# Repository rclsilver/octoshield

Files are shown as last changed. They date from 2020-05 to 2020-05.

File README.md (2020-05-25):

# OctoShield

This Raspberry pi hat can be used with [OctoPrint-Enclosure](https://plugins.octoprint.org/plugins/enclosure/) plugin.

This hat is compatible with Raspberry Pi 2, 3 or 4.

With this hat, you will be able to:
* manage a 30x30 5V fan to regulate the Raspberry Pi temperature
* manage a dual relay module for printer power and a LED strip
* read the temperature of your enclosure with a [DS18B20](https://datasheets.maximintegrated.com/en/ds/DS18B20.pdf) sensor
* cut the power of your printer when some smoke is detected by an external smoke detector or when you press an emergency button

All connectors are [JST XH](https://www.jst-mfg.com/product/pdf/eng/eXH.pdf) to be easier to use.

## Inputs / Outputs

* `GPIO.5` (Output): The fan
* `GPIO.7` (Input): The [DS18B20](https://datasheets.maximintegrated.com/en/ds/DS18B20.pdf) sensor
* `GPIO.27` (Input): The power button to toggle printer power
* `GPIO.17` (Output): The signal to the relay which manages the printer power
* `GPIO.4` (Input): The LED button to toggle LED strip power
* `GPIO.3` (Output): The signal to the relay which manages the LED strip power
* `GPIO. 6` (Input): The emergency signal to turn off the printer power

## Power

The board works with a *5V DC* power. The power supply must be connected to `J1` connector:

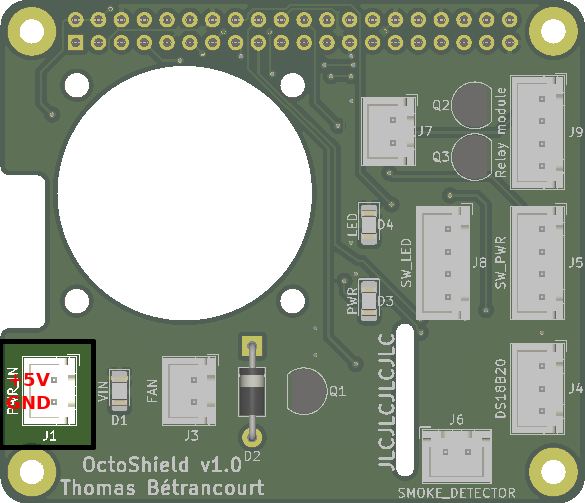
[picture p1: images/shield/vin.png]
shield_vin


## Fan

The fan must be connected to `J3` connector:

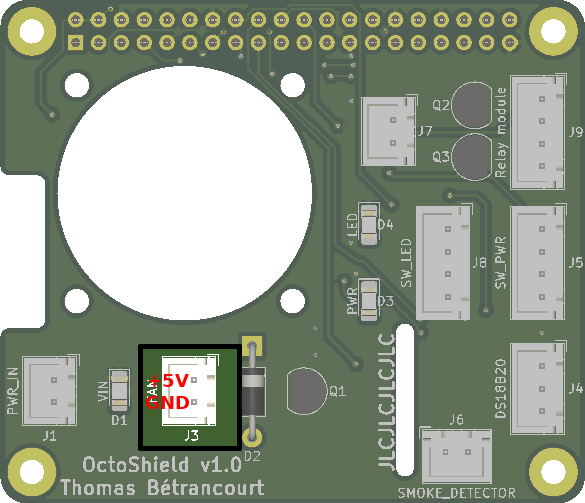
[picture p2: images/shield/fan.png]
shield_fan


The fan can be controlled with the `GPIO.5`. A *HIGH* level turn on the fan.

You can use the provided [script](/fan-control/fan-control.py) and [SystemD service](/fan-control/fan-control.service) to manage the regulate the temperature.

You must use the [SSH](https://www.raspberrypi.org/documentation/remote-access/ssh/) access to enable the service by executing following commands with the `pi` user:

```shell
git clone https://github.com/rclsilver/octoshield.git
sudo cp octoshield/fan-control/fan-control.py /usr/local/bin
sudo cp octoshield/fan-control/fan-control.service /etc/systemd/system/
sudo systemctl daemon-reload
sudo systemctl enable fan-control.service
sudo systemctl start fan-control.service
```

## Temperature sensor

The sensor must be connected to `J4` connector:

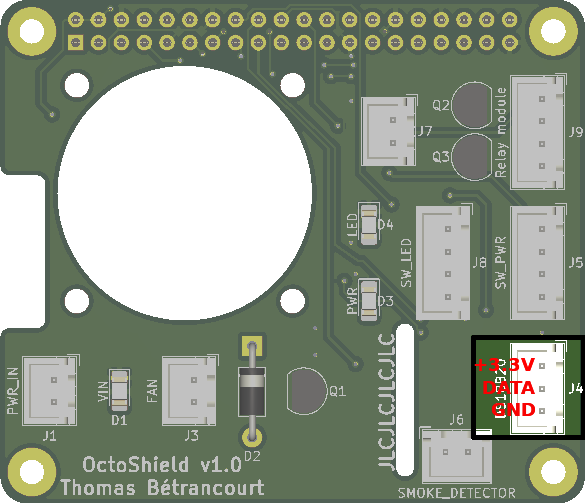
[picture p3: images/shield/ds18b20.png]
shield_ds18b20


Temperature sensor [DS18B20](https://datasheets.maximintegrated.com/en/ds/DS18B20.pdf) can be used with the [1-Wire](https://en.wikipedia.org/wiki/1-Wire) protocol on a Raspberry Pi.

You must enable this interface to be used with the [SSH](https://www.raspberrypi.org/documentation/remote-access/ssh/) access by executing following commands with the `pi` user:

```shell
sudo raspi-config
```

*Note*: Use the direction arrows to navigate in the menu and the *Enter* key to validate.

1. Enter in the `Interfacing Options` menu
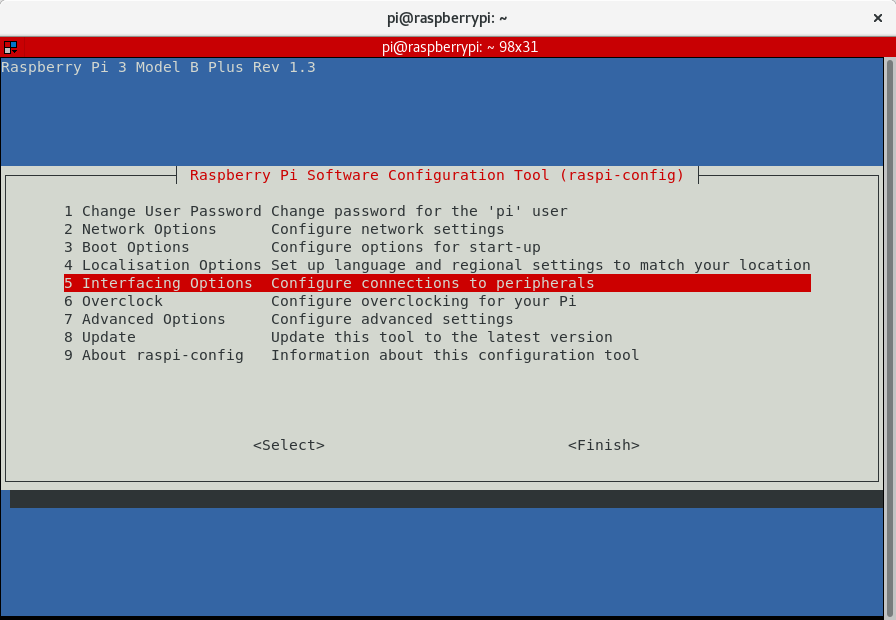
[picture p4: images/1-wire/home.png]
raspi-config_home


1. Enter in the `1-Wire` submenu
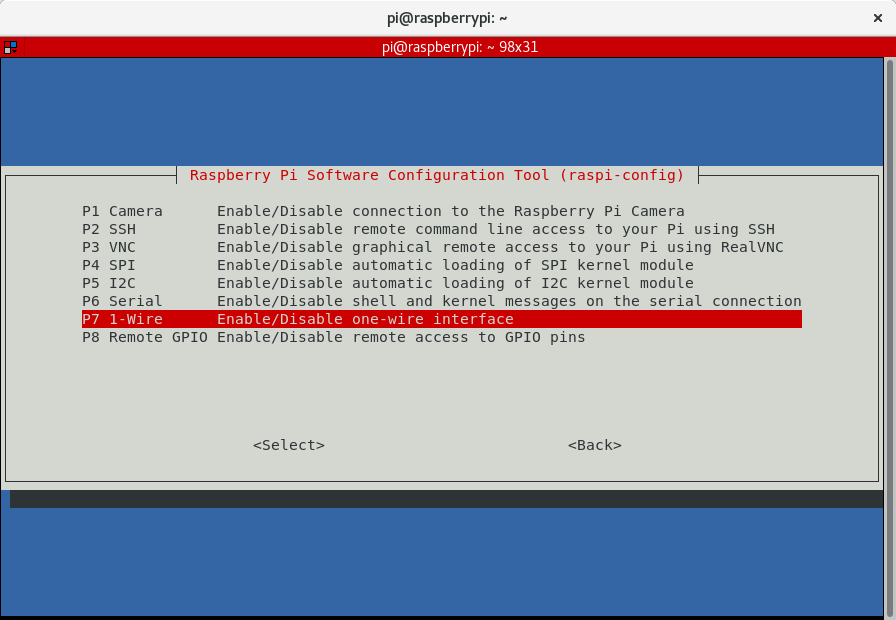
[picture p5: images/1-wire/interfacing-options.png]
raspi-config_interfacing-options


1. Select `Yes` and press the *Enter* key
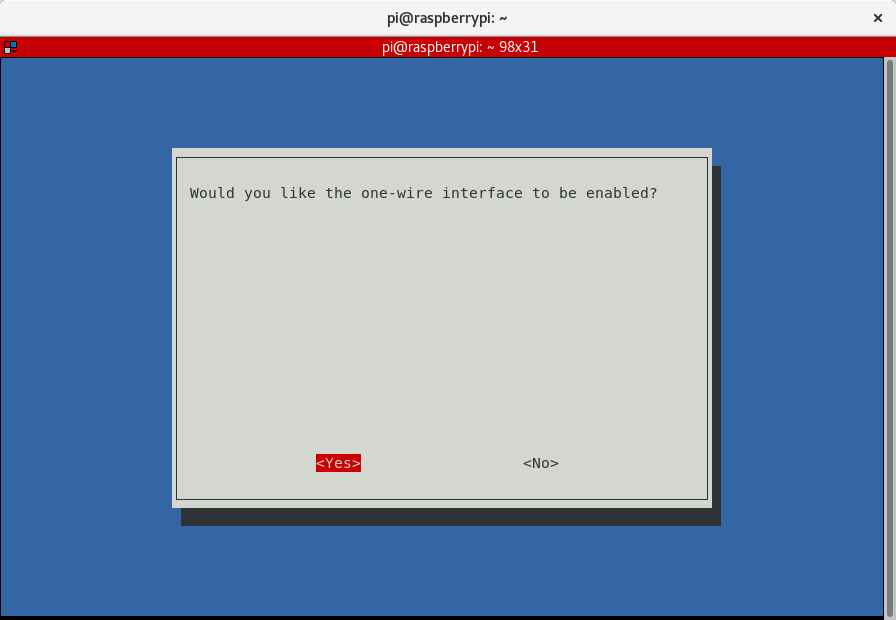
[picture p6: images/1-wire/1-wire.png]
raspi-config_1-wire


1. The interface has been enabled, you can press *Enter* to continue
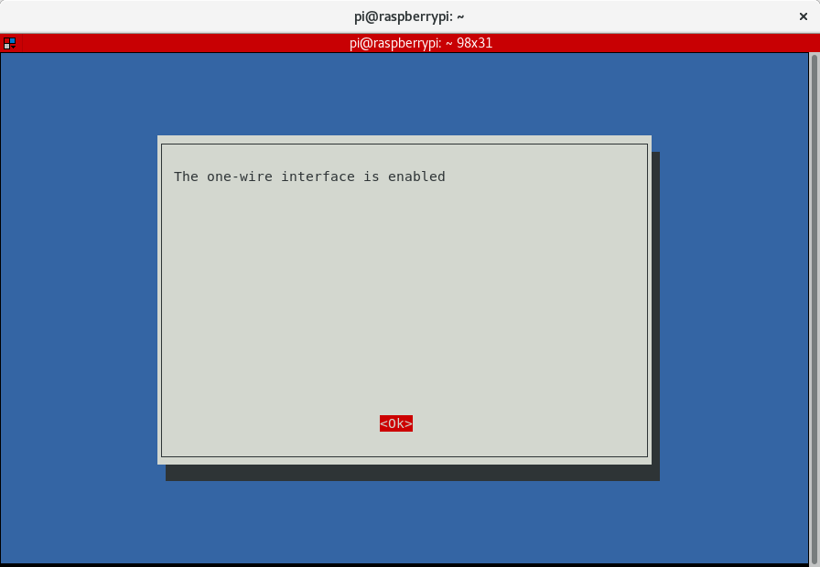
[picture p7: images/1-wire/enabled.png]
raspi-config_enabled


1. You can now select `Finish` with the *Right arrow* key
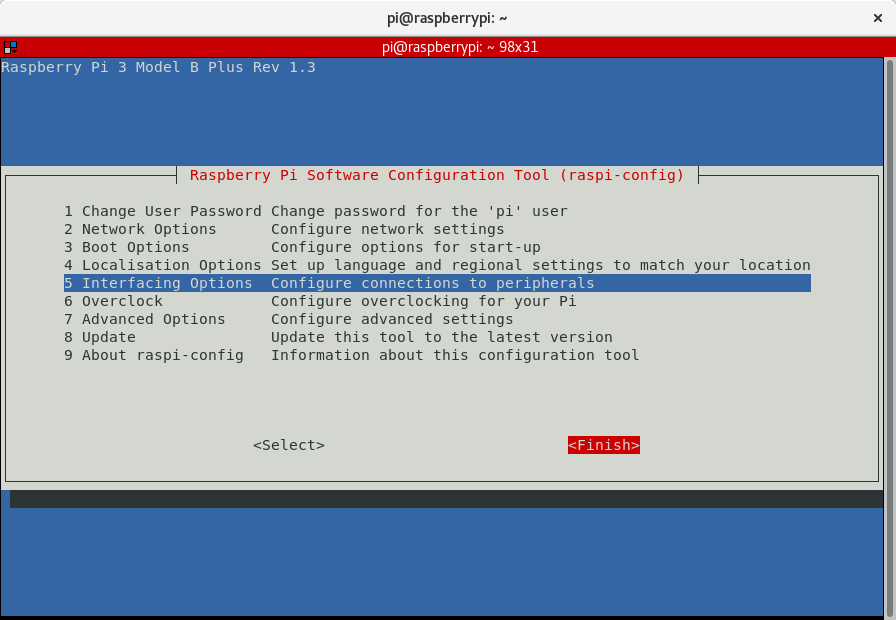
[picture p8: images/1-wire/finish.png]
raspi-config_finish


1. You have to reboot the Raspberry pi
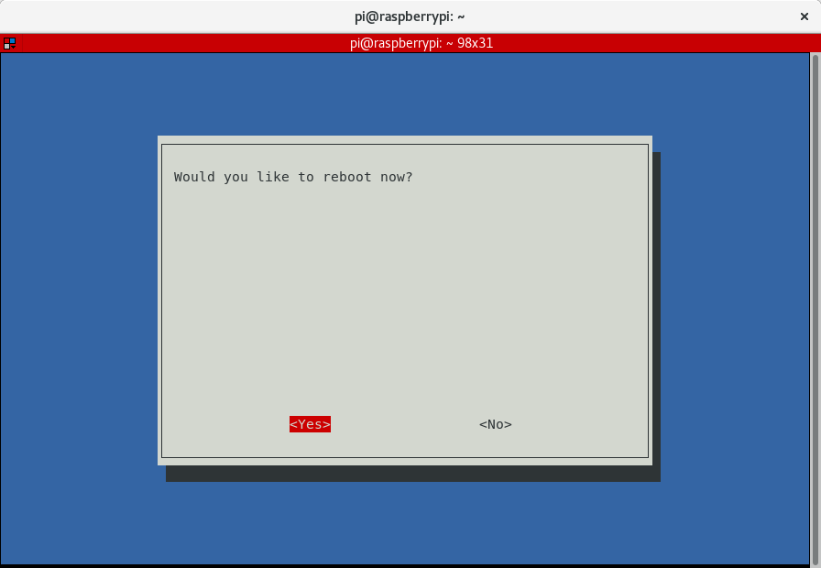
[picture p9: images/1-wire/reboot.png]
raspi-config_reboot


You will need to obtain your temperature device id by executing the following command:

```shell
cat /sys/devices/w1_bus_master1/*/name
```

This will print the ID if all is working fine. If nothing is printed, please check your installation.

Now, in the [OctoPrint-Enclosure](https://plugins.octoprint.org/plugins/enclosure/) plugin settings, you can add your sensor by adding a new Input and following this screenshot:

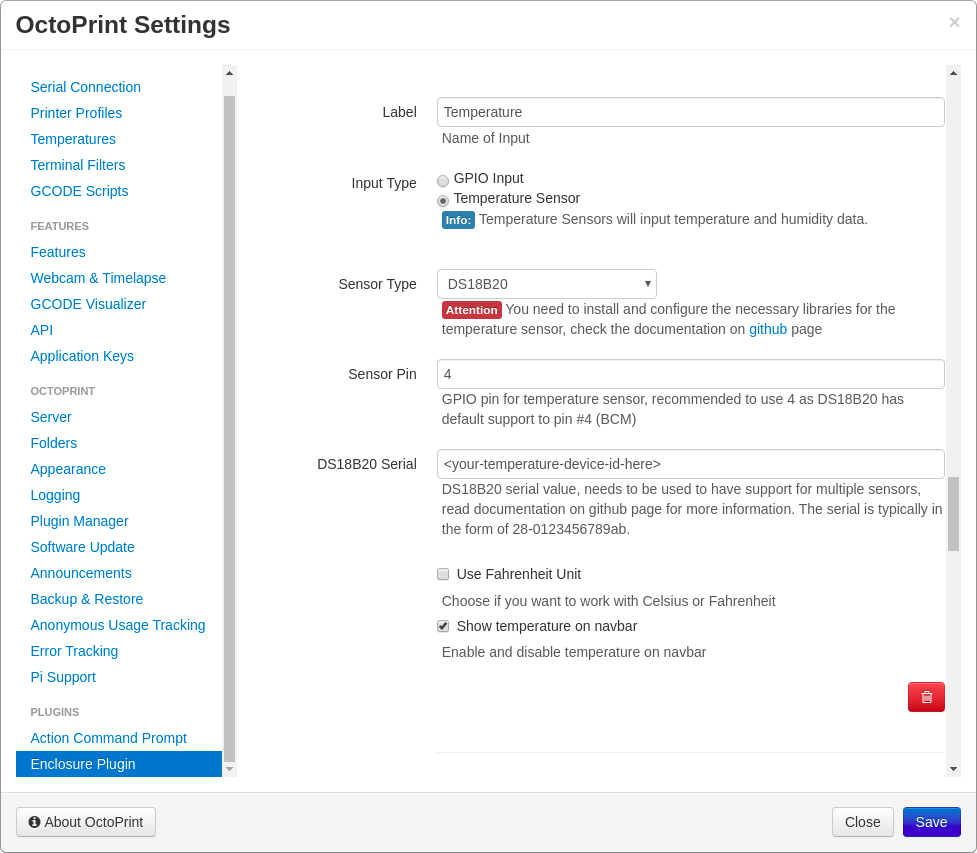
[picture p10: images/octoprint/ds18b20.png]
octoprint_ds18b20


## Printer power

The power switch must be connected to `J5` connector:

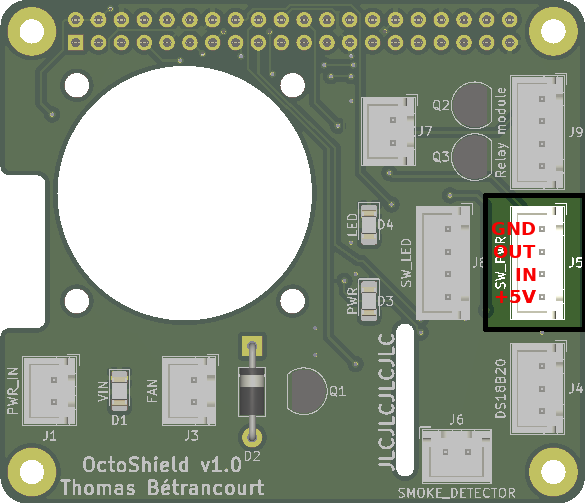
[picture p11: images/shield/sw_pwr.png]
shield_sw_pwr


When `+5V` and `IN` pins are connected, a *LOW* level is transmitted to the `PWR` pin of `J9` and power of printer is turned on. In this case, `OUT` pin is powered by a *5V DC* power to turn on a light signal.

### OctoPrint

Now, in the [OctoPrint-Enclosure](https://plugins.octoprint.org/plugins/enclosure/) plugin settings, you can manage the printer power relay following those screenshots.

#### Input

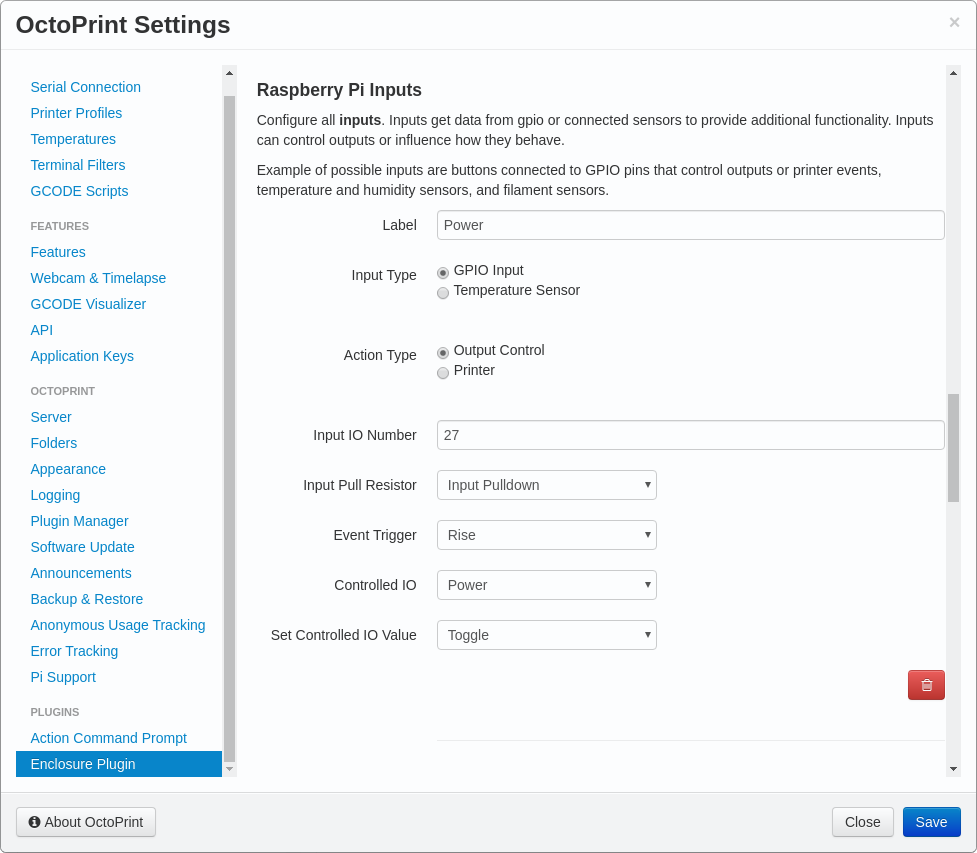
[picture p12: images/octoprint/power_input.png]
octoprint_pwr_input


#### Output

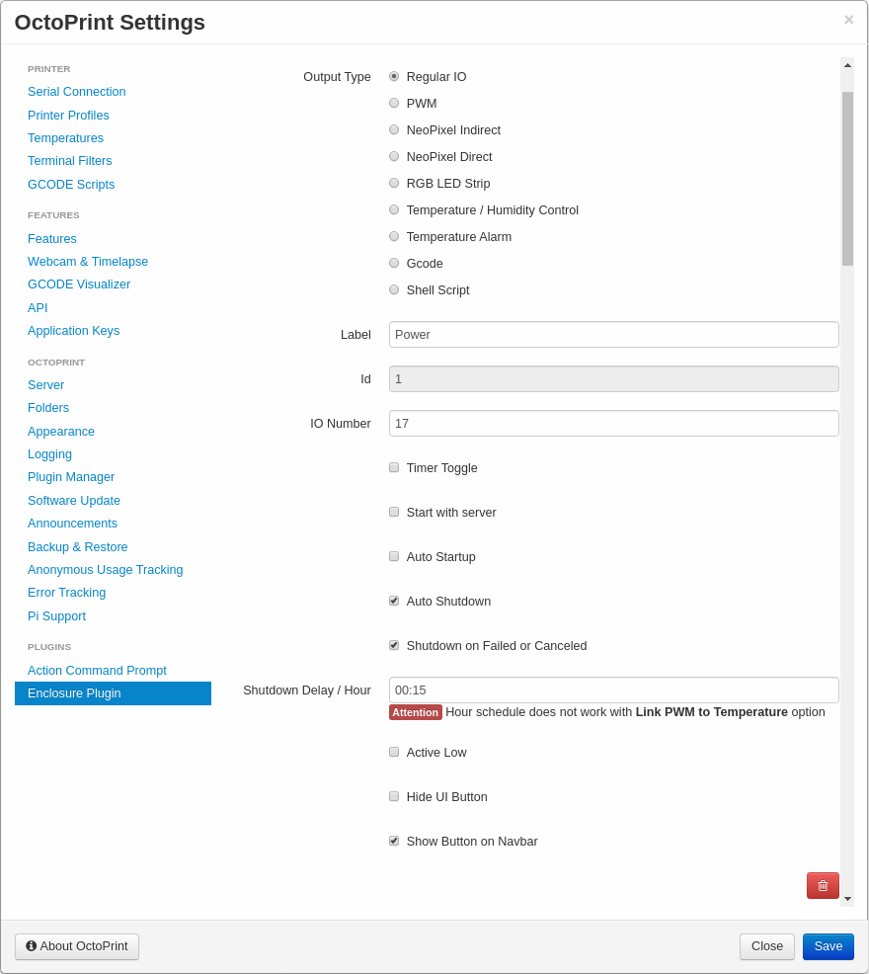
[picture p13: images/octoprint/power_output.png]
octoprint_pwr_output


## LED strip power

The LED strip switch must be connected to `J8` connector:

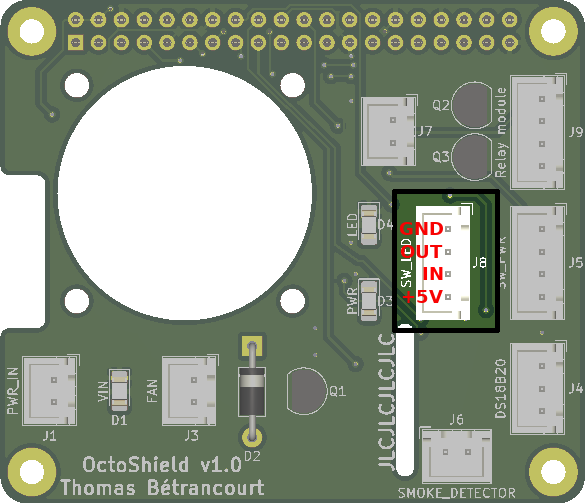
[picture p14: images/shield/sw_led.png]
shield_sw_led


When `+5V` and `IN` pins are connected, a *LOW* level is transmitted to the `LED` pin of `J9` and power of LED strip is turned on. In this case, `OUT` pin is powered by a *5V DC* power to turn on a light signal.

### OctoPrint

Now, in the [OctoPrint-Enclosure](https://plugins.octoprint.org/plugins/enclosure/) plugin settings, you can manage the LED strip power relay following those screenshots.

#### Input

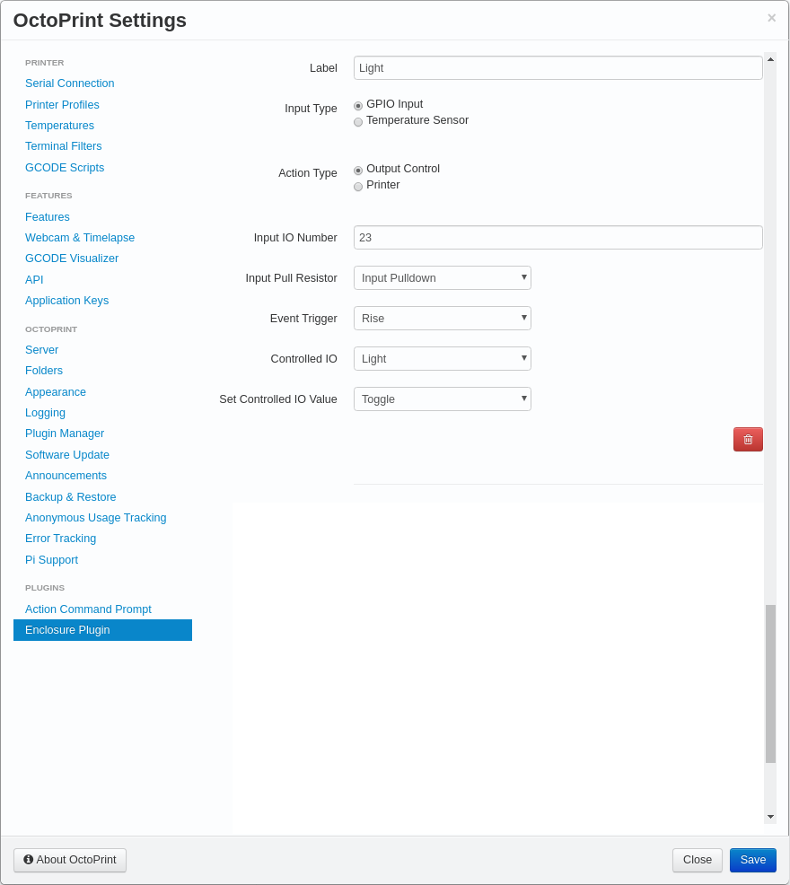
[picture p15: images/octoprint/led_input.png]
octoprint_led_input


#### Output

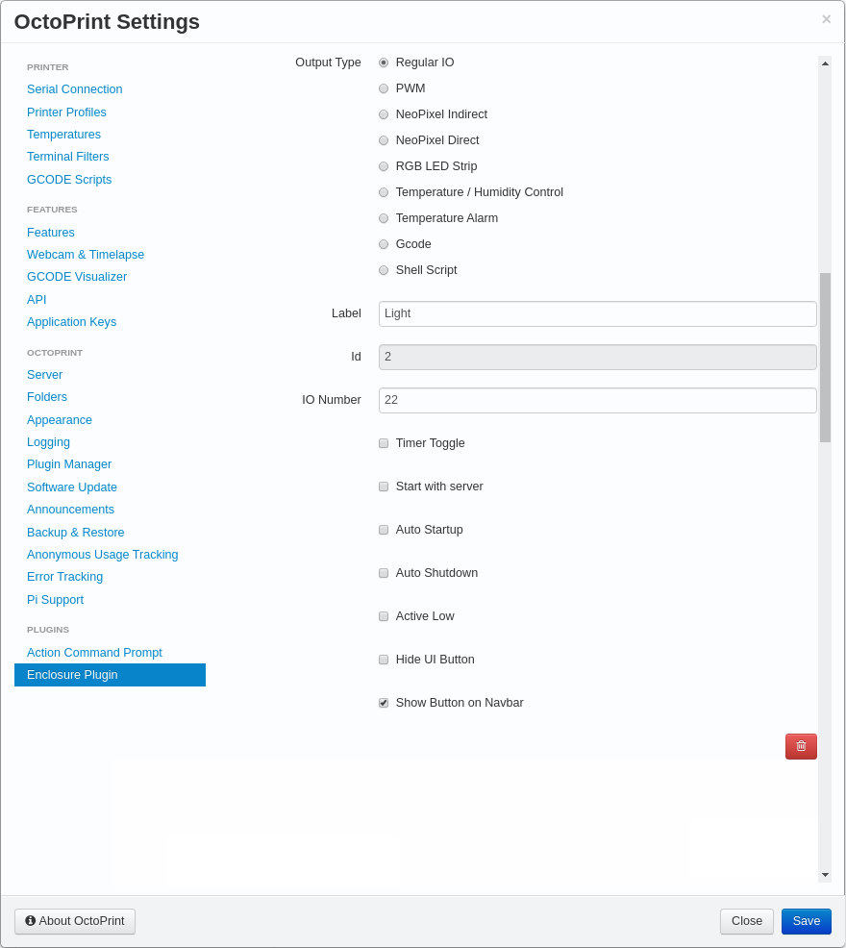
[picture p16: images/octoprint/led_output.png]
octoprint_led_output


## Smoke detector / Emergency button

You can use both a smoke detector or an emergency button to power down the printer.

### Smoke detector

Most of detectors send *9V DC* power when it detects some smoke. You must find points on your and connect them on `J8` connector:

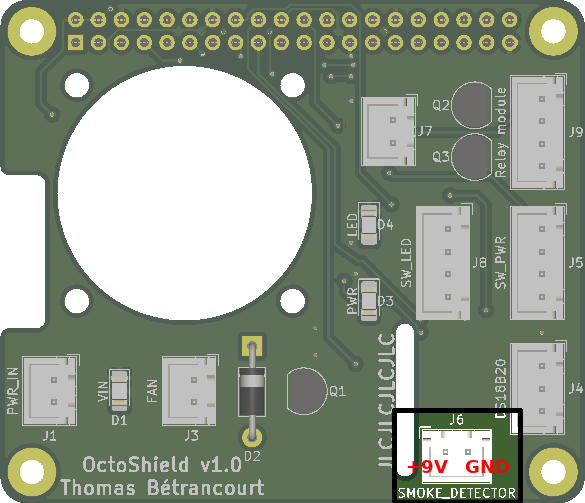
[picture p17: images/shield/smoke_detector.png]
shield_smoke_detector


When the detector is detecting smoke, a *HIGH* level is transmitted to the `GPIO.6`. You have to tell OctoPrint to turn off the printer.

### Emergency button

The emergency button must be connected to `J7` connector:

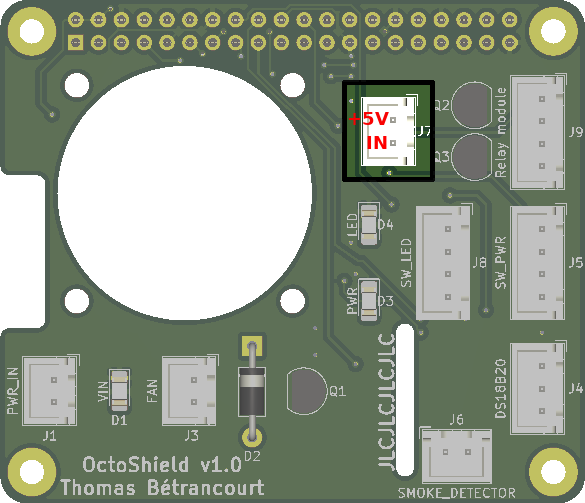
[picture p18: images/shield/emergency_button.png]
shield_sw_led


When `+5V` and `IN` pins are connected, a *HIGH* level is transmitted to the `GPIO.6`. You have to tell OctoPrint to turn off the printer.

### OctoPrint

Now, in the [OctoPrint-Enclosure](https://plugins.octoprint.org/plugins/enclosure/) plugin settings, you can add your emergency input following this screenshot.

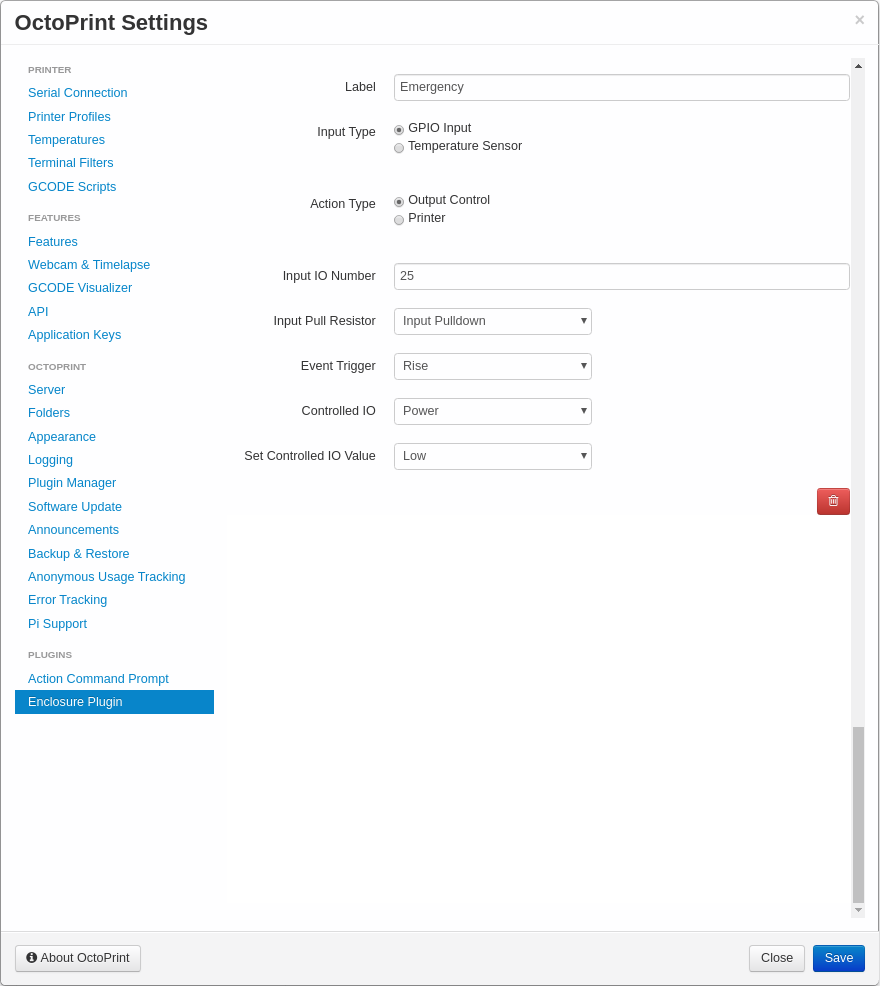
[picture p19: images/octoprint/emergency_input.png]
octoprint_emergency_input


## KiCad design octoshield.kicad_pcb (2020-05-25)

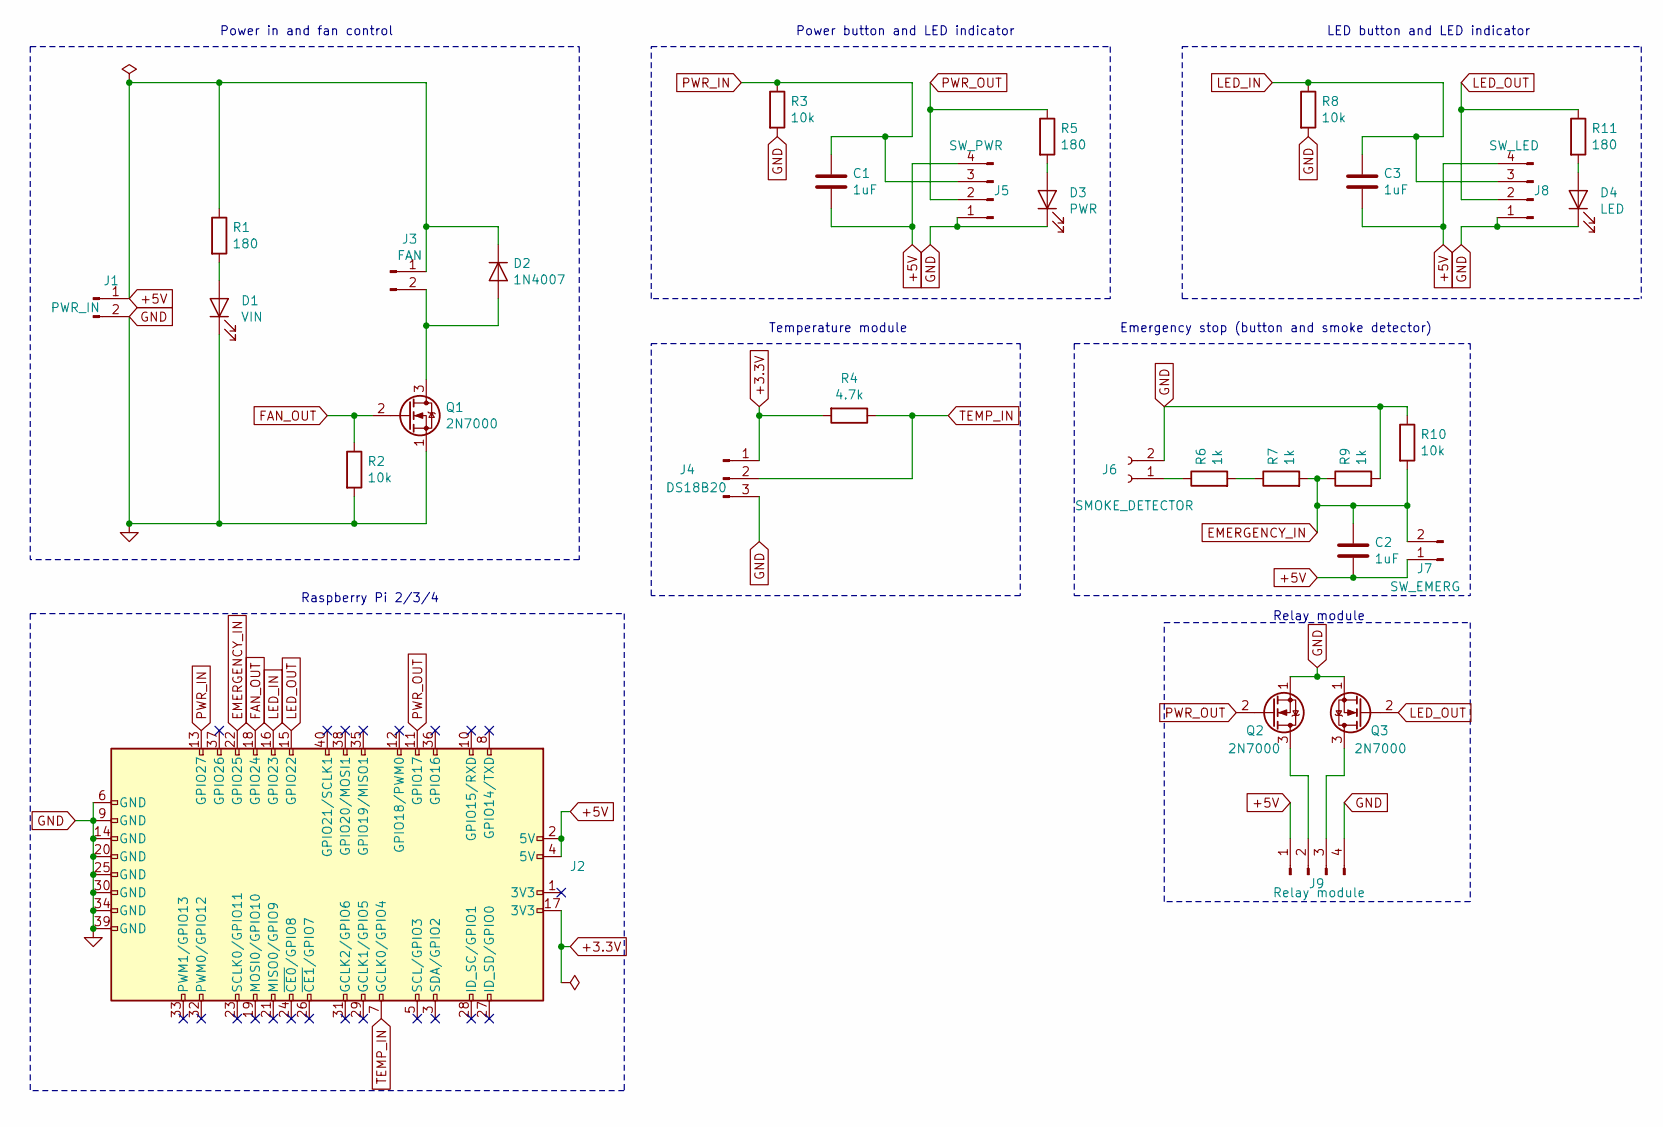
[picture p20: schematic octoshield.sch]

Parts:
C1, C2, C3: 1uF; C_1206_3216Metric_Pad1.42x1.75mm_HandSolder
D1: VIN; LED_1206_3216Metric_Pad1.42x1.75mm_HandSolder
D2: 1N4007; D_DO-41_SOD81_P10.16mm_Horizontal
D3: PWR; LED_1206_3216Metric_Pad1.42x1.75mm_HandSolder
D4: LED; LED_1206_3216Metric_Pad1.42x1.75mm_HandSolder
J1: PWR_IN; JST_XH_B2B-XH-A_1x02_P2.50mm_Vertical
J2: Raspberry Pi 2/3/4; PinSocket_2x20_P2.54mm_Vertical
J3: FAN; JST_XH_B2B-XH-A_1x02_P2.50mm_Vertical
J4: DS18B20; JST_XH_B3B-XH-A_1x03_P2.50mm_Vertical
J5: SW_PWR; JST_XH_B4B-XH-A_1x04_P2.50mm_Vertical
J6: SMOKE_DETECTOR; JST_XH_B2B-XH-A_1x02_P2.50mm_Vertical
J7: SW_EMERG; JST_XH_B2B-XH-A_1x02_P2.50mm_Vertical
J8: SW_LED; JST_XH_B4B-XH-A_1x04_P2.50mm_Vertical
J9: Relay module; JST_XH_B4B-XH-A_1x04_P2.50mm_Vertical
Q1, Q2, Q3: 2N7000; TO-92_Inline
R1, R5, R11: 180; R_1206_3216Metric_Pad1.42x1.75mm_HandSolder
R2, R3, R8, R10: 10k; R_1206_3216Metric_Pad1.42x1.75mm_HandSolder
R4: 4.7k; R_1206_3216Metric_Pad1.42x1.75mm_HandSolder
R6, R7, R9: 1k; R_1206_3216Metric_Pad1.42x1.75mm_HandSolder

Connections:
+3.3V: J2.17 (3V3), J4.1, R4.2
+5V: C1.2, C2.1, C3.2, D2.1 (K), J1.1, J2.2 (5V), J2.4 (5V), J3.1, J5.4, J7.1, J8.4, J9.1, R1.1
EMERGENCY_IN: C2.2, J2.22 (GPIO25), J7.2, R7.2, R9.1, R10.2
FAN_OUT: J2.18 (GPIO24), Q1.2 (G), R2.1
GND: D1.1 (K), D3.1 (K), D4.1 (K), J1.2, J2.6 (GND), J2.9 (GND), J2.14 (GND), J2.20 (GND), J2.25 (GND), J2.30 (GND), J2.34 (GND), J2.39 (GND), J4.3, J5.1, J6.2, J8.1, J9.4, Q1.1 (S), Q2.1 (S), Q3.1 (S), R2.2, R3.2, R8.2, R9.2, R10.1
LED_IN: C3.1, J2.16 (GPIO23), J8.3, R8.1
LED_OUT: J2.15 (GPIO22), J8.2, Q3.2 (G), R11.1
unnamed: D1.2 (A), R1.2
unnamed: D2.2 (A), J3.2, Q1.3 (D)
unnamed: D3.2 (A), R5.2
unnamed: D4.2 (A), R11.2
unnamed: J6.1, R6.1
unnamed: J9.2, Q2.3 (D)
unnamed: J9.3, Q3.3 (D)
unnamed: R6.2, R7.1
PWR_IN: C1.1, J2.13 (GPIO27), J5.3, R3.1
PWR_OUT: J2.11 (GPIO17), J5.2, Q2.2 (G), R5.1
TEMP_IN: J2.7 (GCLK0/GPIO4), J4.2, R4.1

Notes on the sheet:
Power button and LED indicator
LED button and LED indicator
Power in and fan control
Temperature module
Emergency stop (button and smoke detector)
Raspberry Pi 2/3/4
Relay module

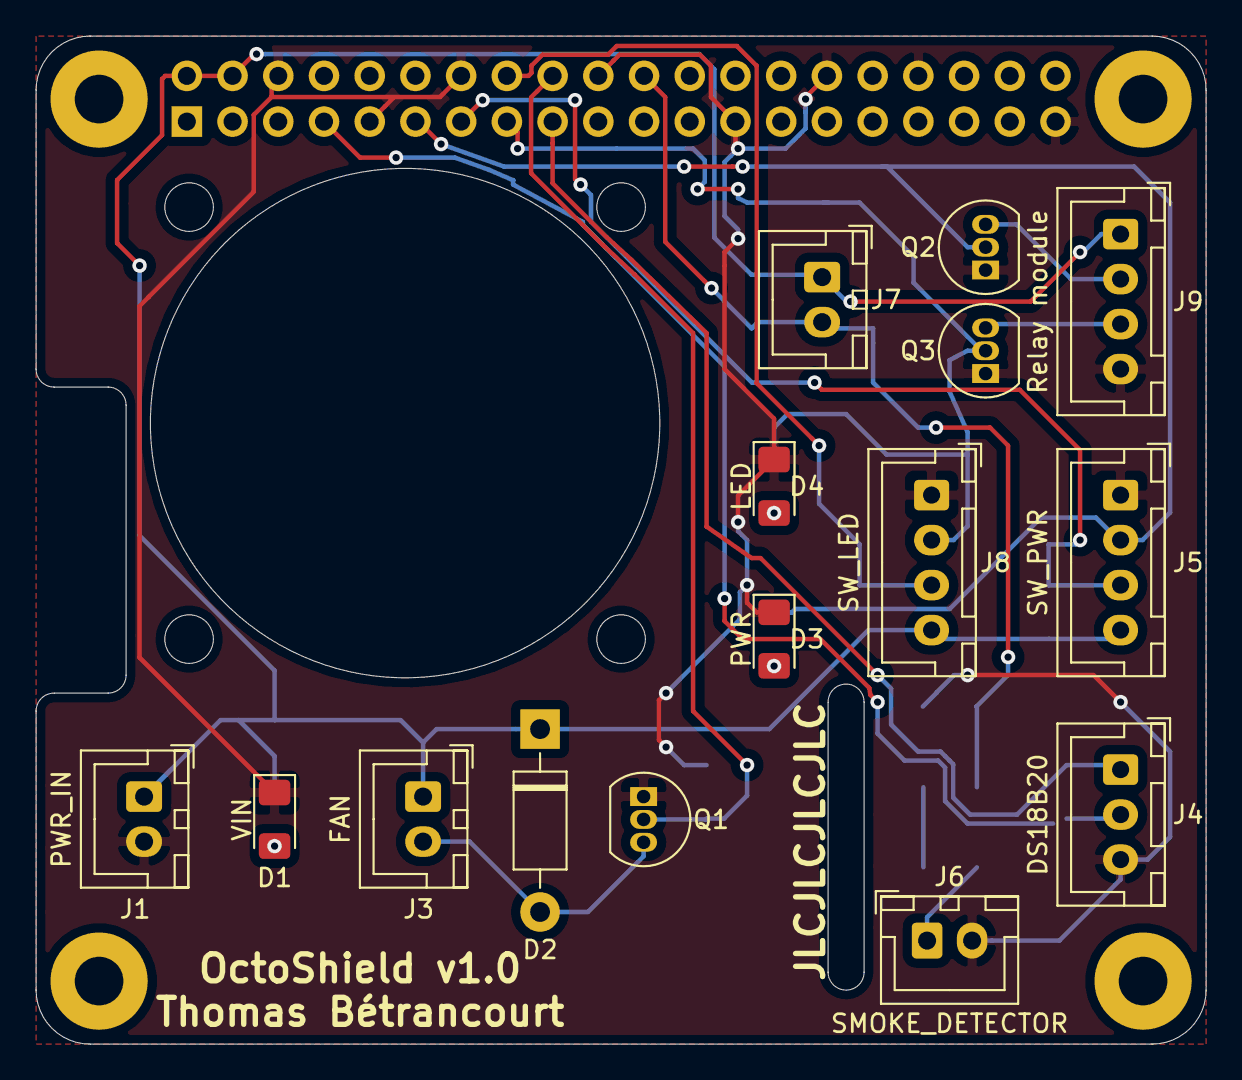
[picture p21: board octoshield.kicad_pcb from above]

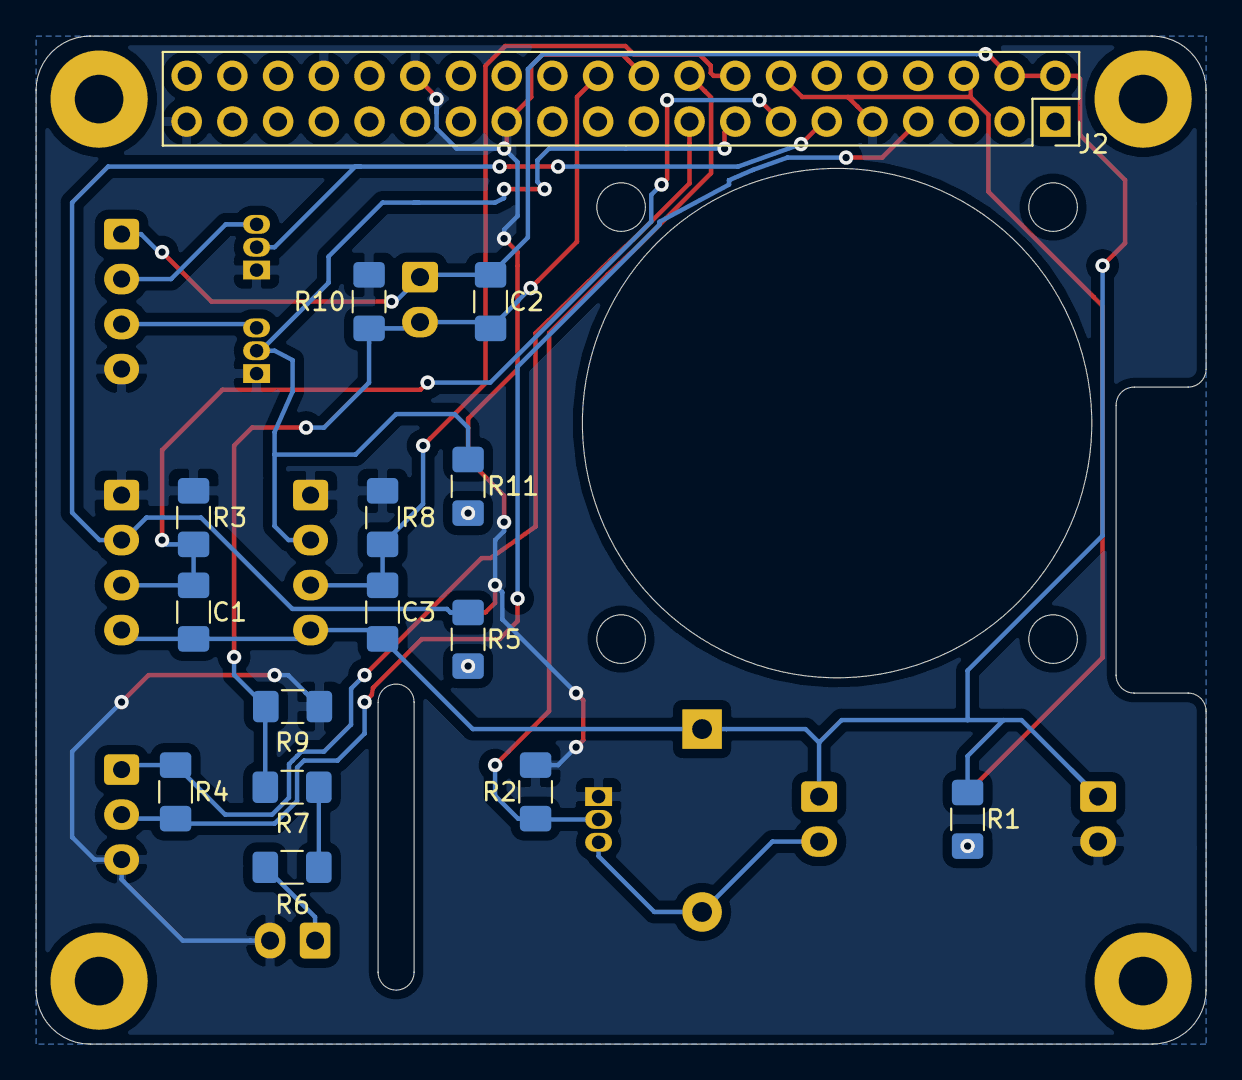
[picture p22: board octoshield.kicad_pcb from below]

Board: 2 copper layers, 65.0 x 56.0 mm, 30 parts (15 on the bottom side), 18 nets.

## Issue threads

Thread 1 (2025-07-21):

ADXL345 Support

Dalarialus, 2025-07-21:
Is there anything that would prevent this hat being used in conjunction with a ADXL345 accelerometer? From what I can see, it doesn't look like there are any obvious pin conflicts with the documentation on [klipper](https://www.klipper3d.org/Measuring_Resonances.html), but I'm still *painfully* new at this!

rclsilver, 2025-07-21:
Hello.

If the needed pin are free (cf the readme) then it is OK.

We can create some pads on the board to make easier to connect your component. AFAIK the ADXL345 needs an i2c channel to work?

rclsilver, 2025-07-22:
Yes, we could add two headers for this usage but IMO, you should check that everything is OK with Klipper, I never used it
